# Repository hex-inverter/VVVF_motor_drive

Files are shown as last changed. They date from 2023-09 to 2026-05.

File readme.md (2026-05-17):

# Three-Phase Induction Motor Controller

The inspiration for this project came from a very characteristic sound in Amsterdam metro trams. During acceleration or braking they make a "shifting gears" sound even though the motors are electric (this sound can also be heard in the demonstration video below).
I became interested in what causes this phenomenon and discovered that the sound is related to the switching behavior and frequency management of inverter-driven AC motors. To better understand these systems, I designed and built a complete three-phase induction motor controller and presented a project for seminar class as part of the course at Faculty of Electrical Engineering, University of Ljubljana.

The project focuses on generating variable-frequency three-phase waveforms using SPWM (Sinusoidal Pulse Width Modulation) and DDS (Direct Digital Synthesis) techniques implemented on an STM32 microcontroller. The controller is capable of driving an asynchronous motor directly from rectified mains voltage while allowing the motor speed to be controlled with a potentiometer.

Here you can find a video demonstration of the final product:

<a href="https://youtu.be/MzE1TKPA2_U?si=Al2wI3Vebfvr4Jmp&t=35">
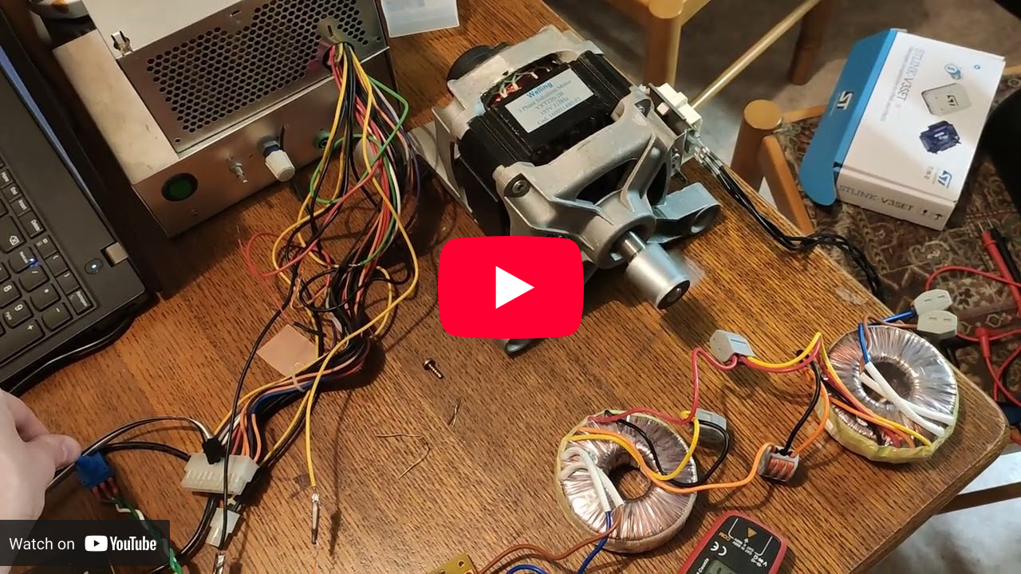
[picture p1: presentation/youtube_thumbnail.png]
    
</a>

## Overview

The controller consists of a mains input stage with EMI filtering, a rectifier that generates a high-voltage DC bus, and a three-phase inverter built using IGBT transistors. The inverter is controlled by an STM32 microcontroller, which generates SPWM drive signals for the motor phases.
Motor speed is adjusted by a potentiometer, while the firmware continuously monitors current and DC bus voltage through ADC measurements. The project also implements different switching strategies to reduce transistor losses at higher output frequencies.

The more in-depth report of the working of the driver can be found in the project report (in Slovenian).

## Hardware

The hardware was designed in KiCad and PCB was etched at home.

<a>
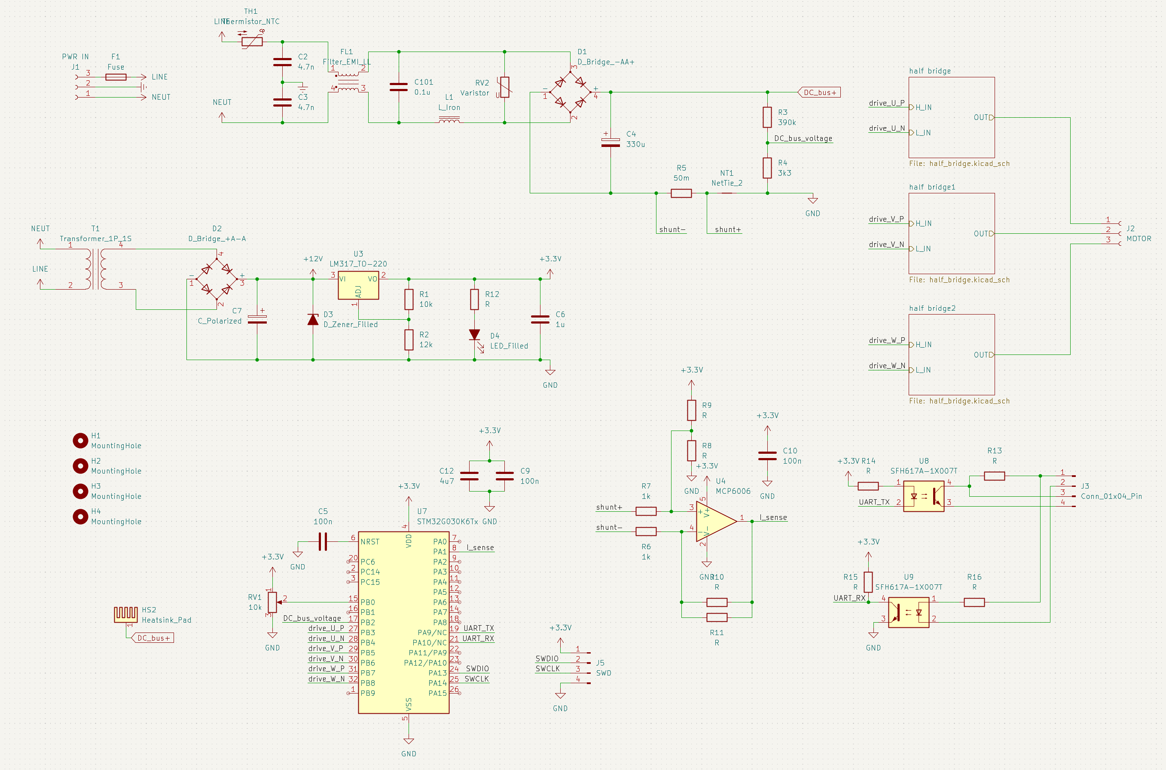
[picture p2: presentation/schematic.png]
    
</a>

Main components:
- EMI filtering
- Mains rectification
- Low-voltage auxiliary power supply
- Three-phase IGBT inverter
- Gate driver circuitry
- Current sensing
- STM32 control circuitry
- Custom PCB

## Firmware

The firmware is written for the STM32G030 microcontroller and generates three-phase SPWM signals for motor control. Frequency generation is implemented using DDS techniques and lookup tables, allowing smooth adjustment of motor speed and phase generation with 120° offsets between phases. The software also handles ADC measurements, frequency management, and inverter switching control.

## Repository Structure

```text
HW/             Hardware design files, schematics, PCB made in KiCad
FW/             STM32 firmware source code
docs/           Documentation and research papers
presentation/   Project report and presentation (sorry, it's in Slovenian)
```

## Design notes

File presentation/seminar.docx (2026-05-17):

Univerza v Ljubljani

Fakulteta za elektrotehniko

Krmilnik trifaznega asinhronskega motorja

Avtor: Boris Trček

Ljubljana, 2023

# 0. Ključne besede

Krmilnik AC motorja, inverter, asinhronski motor, SPWM, DDS

AC motor driver, inverter, asynchronous motor, SPWM, DDS

# 1 Uvod

Nemalokrat sem že opazil, da se nekateri izmenični motorji pri pospeševanju oddajajo nenavaden zvok. Ta namreč med naraščanjem piskanja preskoči na nižjo frekvenco, od koder se ponovno viša. Ponavadi se ta proces tudi večkrat ponovi. Pogosto ga je mogoče slišati pri zaviranju ali pospeševanju tramvajev ali vlakov na podzemnih železnicah. Zanimalo me je zakaj do tega pojava pride, zato sem se odločil da bom za projekt pri predmetu Seminar iz elektronike naredil krmilnik trifaznega motorja.

# 2 Načrtovane specifikacije naprave

Za napravo sem postavil sledeče cilje:

- krmiliti mora trifazni motor s podanimi specifikacijami; nominalna napetost 195V, nominalna frekvenca 310 Hz,
- napajati se mora z omrežno napetostjo 230V 50 Hz,
- delovati mora tako, da se da program enostavno prilagoditi drugemu večfaznemu motorju s spremembo konstant,
- hitrost vrtenja motorja je mogoče krmiliti s potenciometrom.

# 3 Finančni plan

Eden izmed glavnih ciljev projekta je čim cenejša izvedba. Na podlagi tega sem se ubral okolju prijaznejšo rešitev in veliko komponent pridobil z odsluženih vezij starih gospodinjskih aparatov in ostalih naprav.

# 4 Sheme vezja naprave

Spodnji sliki prikazujeta blokovno shemo in shemo krmilnika motorja.

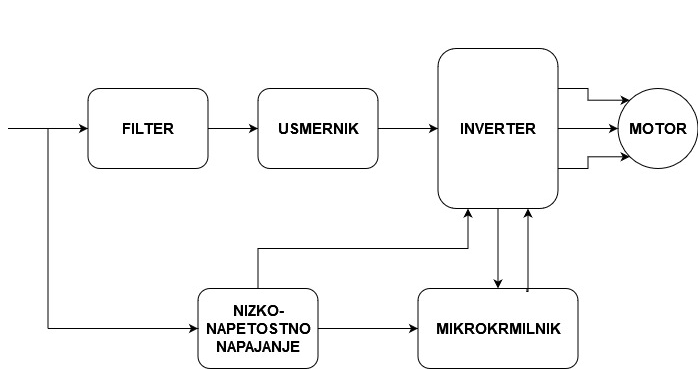
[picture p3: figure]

Slika 1: Blokovna shema


Slika 2: Celotna shema vezja

## 4.1 Filter

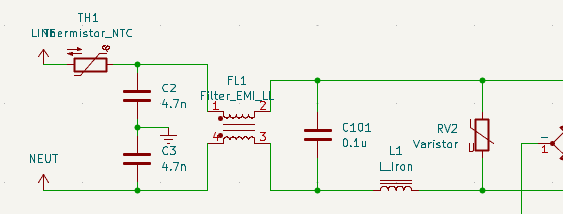
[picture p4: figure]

Slika 3: Filtrirni del vezja

Naprava je napajana z omrežno napetostjo. Takoj pri vhodu se nahajajo filtri, da zmanjša tiste motnje, ki prihajajo v napravo, kot tudi tiste, ki jih naprava generira. NTC termistor z povečano upornostjo preprečuje povečan vhodni tok, ki nastane zaradi polnjenja kondenzatorjev ob zagonu. Za njim dva kondenzatorja tipa Y vrednosti 4,7 nF in dušilka filtrirajo sofazne motnje. Nato kondenzator tipa X velikosti 100 nF zmanjša medfazne motnje. S pomočjo dušilke L1 blažimo tokovne špice, ki nastanejo zaradi polnjenja kondenzatorjev. Z varistorjem RV2 omejimo napetostne sunke.

## 4.2 Usmernik

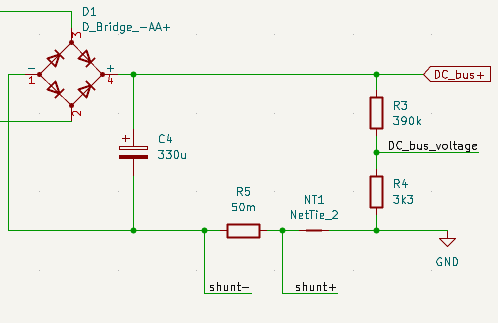
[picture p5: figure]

Slika 4: Usmernik

Usmerniški del vezja sestavljata polnovalni mostiščni usmernik, ki iz sinusnega signala ustvari pozitivno napetost, to pa nato zgladimo z elektrolitskim kondenzatorjem vrednosti 330 µF. Tako pridobimo enosmerno napetostno linijo z amplitudo 325 V, s katero napajamo inverterski del vezja.

## 4.3 Inverter

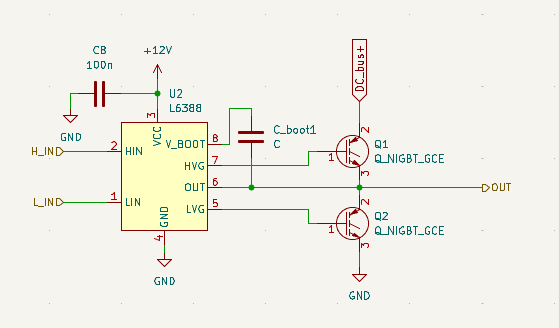
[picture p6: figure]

Slika 5: Inverterski del vezja

Inverter sestavljajo 3 pari IGBT STGP10NC60. Ti tranzistorji imajo v primerjavi z MOSFET nižke izgube in hitrejše preklapljanje. Ker se na njih kljub temu izgublja veliko energije, so skupaj z Grietzovim mostičem usmerniškega dela vezja pritrjeni na hladilna rebra. Tranzistorje krmili mikrokrmilnik preko IGBT krmilnikov. Ta omogoča, da z enim čipom krmilimo vrata obeh tranzistorjev hkrati, kljub temu da lahko napetosti dosežejo tudi do 600V. Omogočajo hitro preklapljanje tranzistorjev, hkrati pa onemogočajo, da bi bila odprta oba tranzistorja hkrati. Takrat bi čez njiju stekel visok tok, zaradi česar bi prišlo do poškodb.

Na srednji odcep vsakega izmed parov tranzistorjev je povezana faza motorja.

## 4.4 Nizkonapetostno napajanje

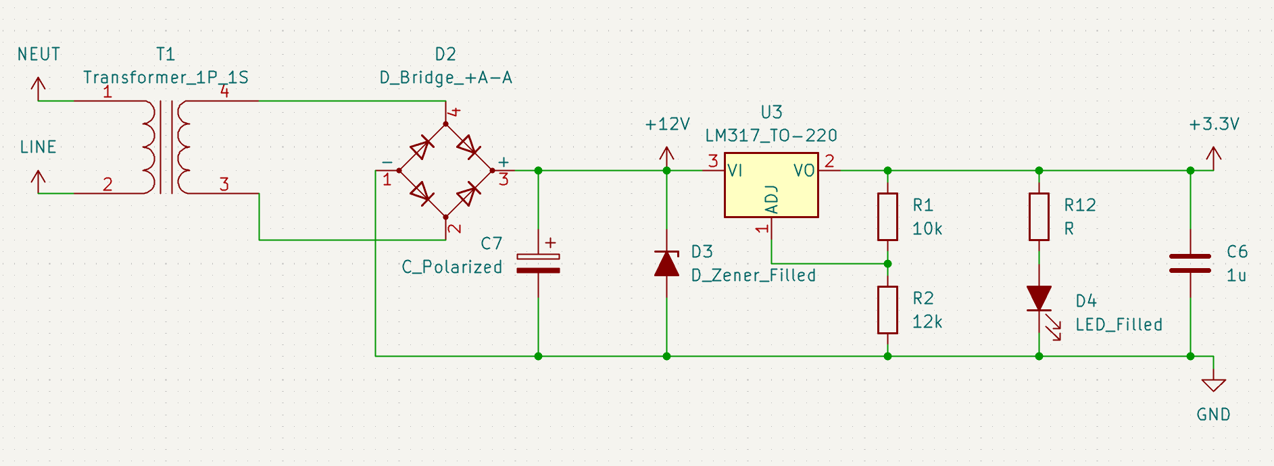
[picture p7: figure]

Slika 6: nizkonapetostno napajanje

S pomočjo transformatorja dobimo iz omrežne napetosti tudi napetost 12V, ki je zglajena in usmerjena s pomočjo polnovalnega mostiščnega usmernika in kondenzatorja. Ker lahko transformator generira tudi višje napetosti, če je premalo obremenjen, sem dodal tudi 15 V zenerjevo diodo. Ta napetost je nato uporabljena za napajanje IGBT krmilnikov in mikrokrmilnika preko linearnega regulatorja, ki zniža napetost na 3.3V.

## 4.5 Mikrokrmilnik

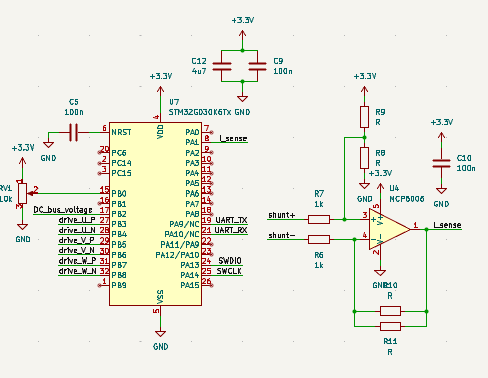
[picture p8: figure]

Slika 7: Mikrokrmilniški del vezja z periferijo

Mikrokrmilnik STM32G030K6T krmili odpiranje in zapiranje tranzistorjev z algoritmom opisanim v naslednjem poglavju glede na željeno frekvenco, ki jo določimo s pozicijo potenciometra. Mikrokrmilnik prav tako upošteva povratno informacijo o toku, ki jo dobi preko tokovnega merilnega upora in operacijskega ojačevalnika, ter napetosti na usmerniku, ki jo izmeri z uporovnega delilnika.

# 5. Tiskano vezje

Spodnje slike prikazujejo zgornjo in spodnjo stran tiskanega vezja, ter končni produkt.

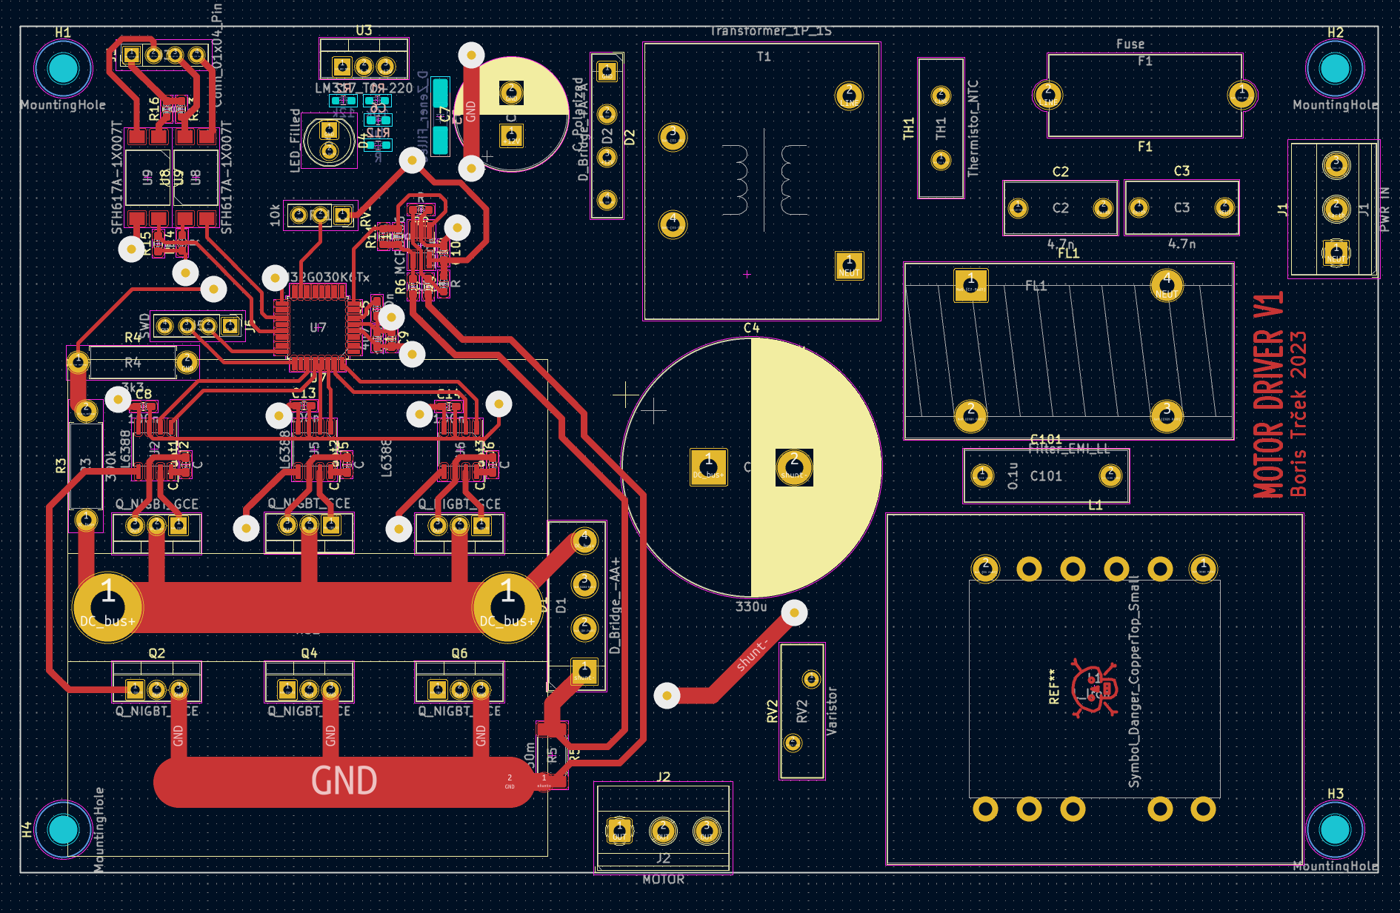
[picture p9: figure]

Slika 8: Zgornja stran tiskanega vezja

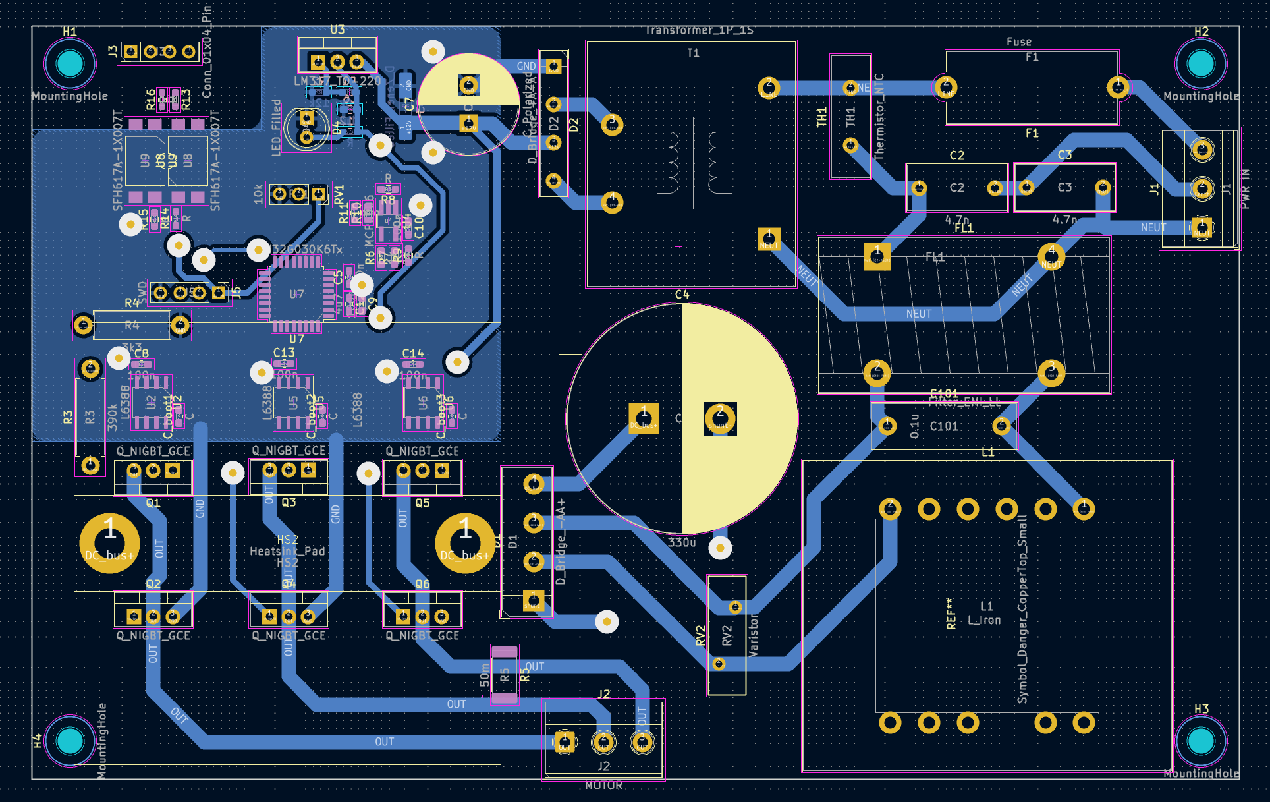
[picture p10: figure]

Slika 9: Spodnja stran tiskanega vezja

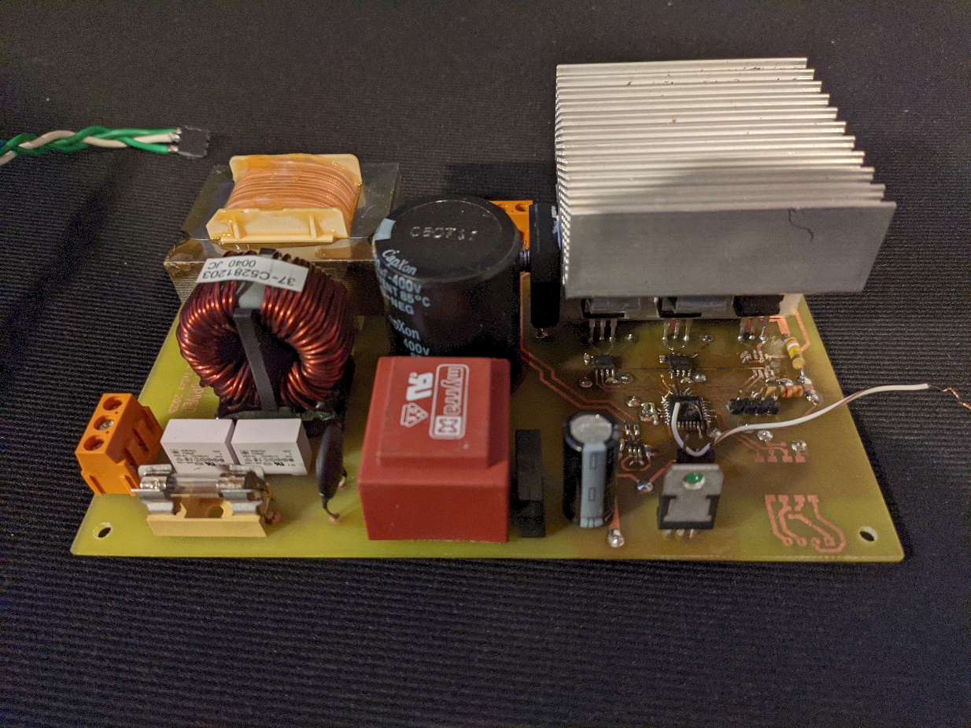
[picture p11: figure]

Slika 10: končni izdelek

# 6. Opis delovanja

Pri krmiljenju motorja z tranzistorji nastane problem, če ga želimo krmiliti z sinusno obliko napetosti. Takrat so namreč tranzistorji delno odprt, motor pa lahko predstavlja visoko breme. Zato se tranzistorji močno segrevajo in lahko tudi pregorijo. Namesto tega se tranzistorje krmili tako, da so ti popolnoma odprti ali zaprti. Da dobimo približek sinusne napetosti pod temi pogoji, moramo uporabiti PWM signal, katerega širina je določena z amplitudo sinusnega signala v določenem časovnem odseku.

## 6.1 SPWM

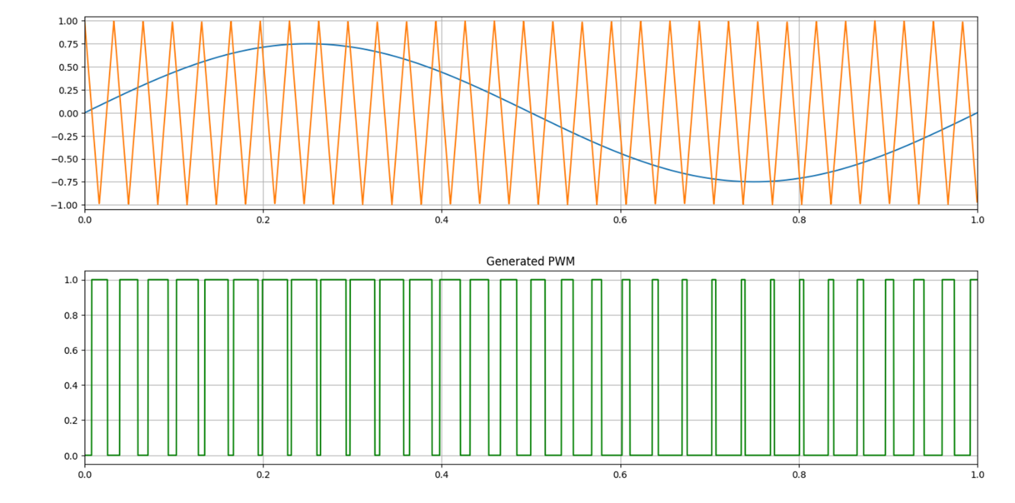
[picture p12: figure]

Slika 11: Generiranje SPWM signala

Postopek za pridobivanje SPWM (Sinusi PWM) signala je razviden iz slike zgornje slike.

Oba tranzistorja se krmili s tem signalom, pri tem pa se signal za krmiljenje spodnjega tranzistorja invertira. Zgornji tranzistor se torej odpre, kadar je sinusni signal večji od vrednosti trikotnega signala, v nasprotnem primeru pa se odpre spodnji tranzistor. Če bi ta signal integrirali po času, bi dobili sinusu podoben signal.

## 6.2 Prestavljanje

Če želimo povečevati hitrost vrtenja motorja, se mora spreminjati frekvenca krmilnega SPWM signala. Tako pridemo do novega problema. Pri višjih frekvencah se na enako gostoto trikotnih signalov znotraj ene periode sinusnega signala tranzistorji pogosteje preklopijo, kar pa poveča tudi izgube na njih, saj so več časa v linearnem področju. Problem je mogoče videti na spodnji sliki.

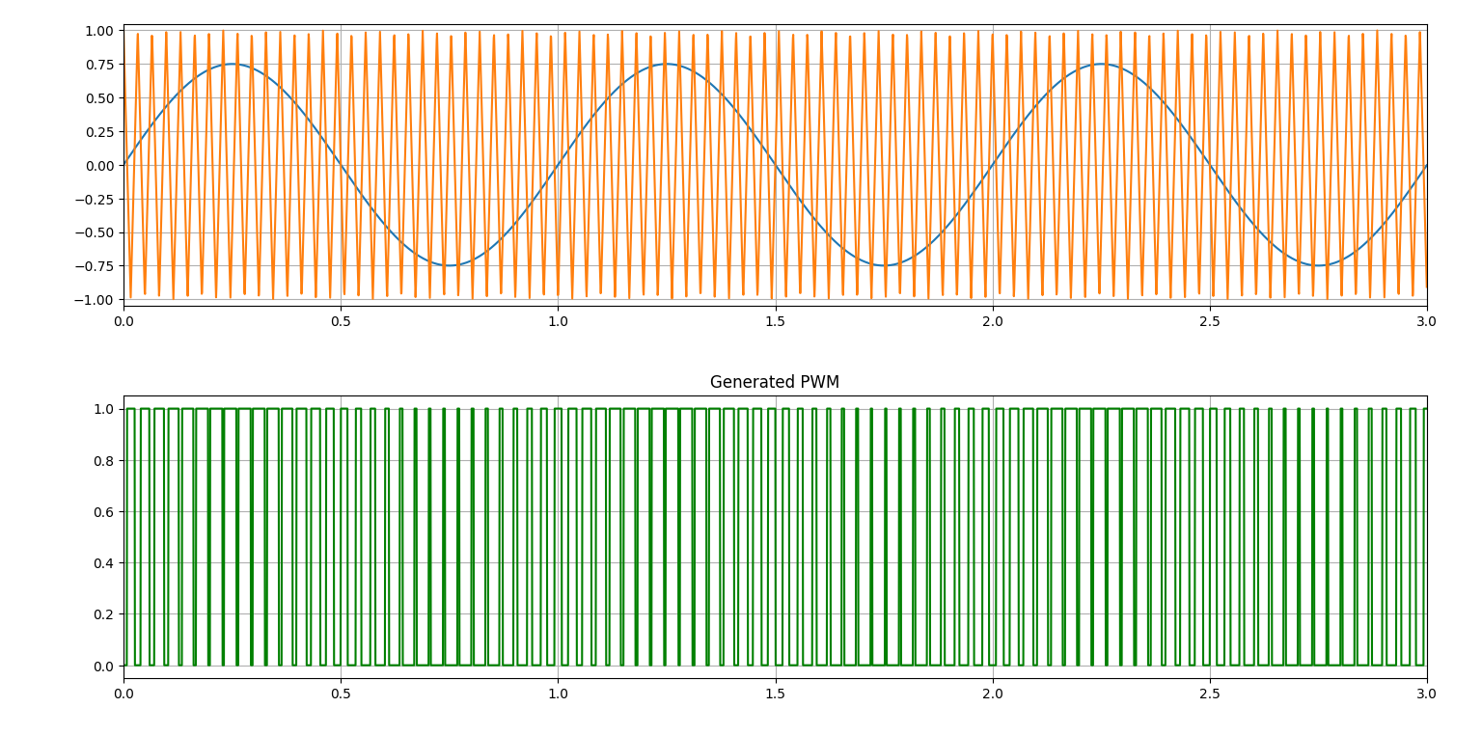
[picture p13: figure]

Slika 12: Primerjava gostote preklopov pri previsokem razmerju period trikotnega in sinusnega signala

Temu se izognemo tako, da zmanjšamo število trikotnikov na periodo sinusnega signala. Temu pojavu se reče "prestavljanje", ki ga je mogoče tudi slišati. Spodnja slika prikazuje kako izgleda izhodni signal pri zmanjšanju razmerja frekvenc signalov.

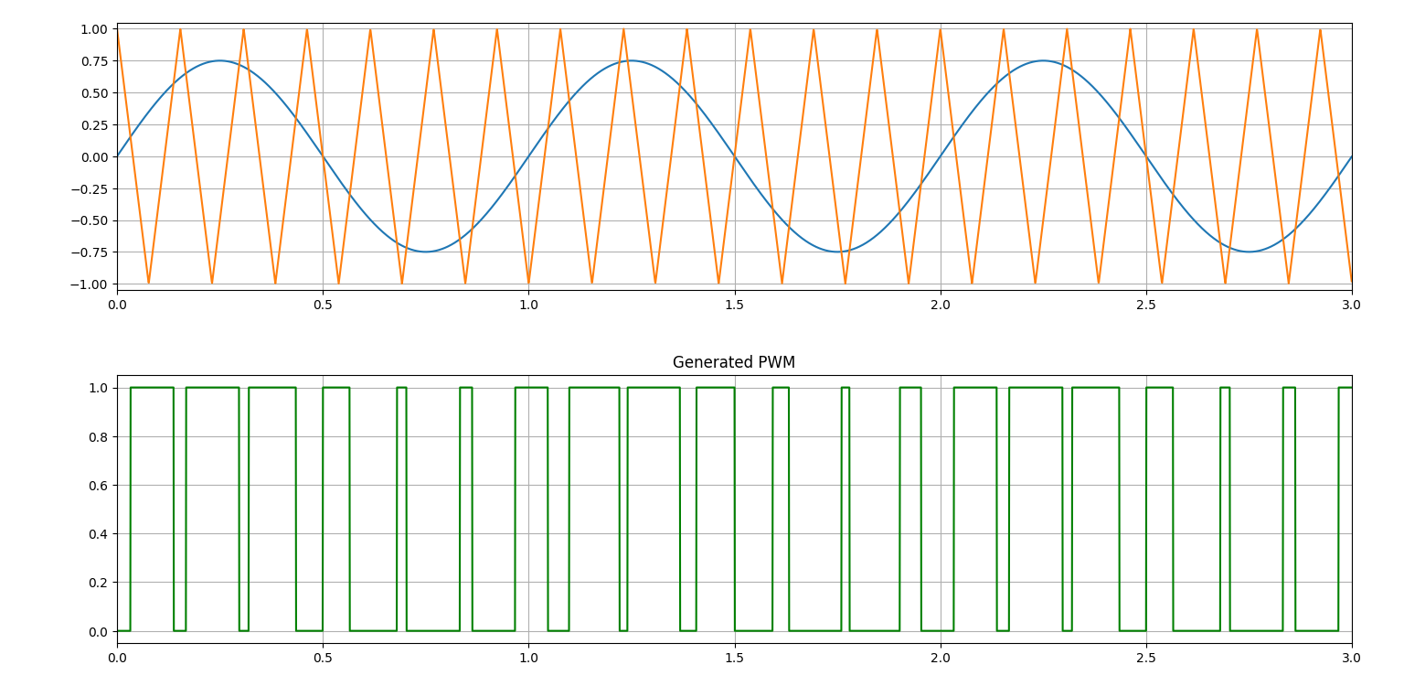
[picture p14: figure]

Slika 13: Primerjava gostote preklopov pri znižanem razmerju period trikotnega in sinusnega signala

## 6.3 Direktna digitalna sinteza (DDS)

DDS (ang. Direct digital synthesis) je metoda za generiranje poljubnega periodičnega signala (pogosto sinusnega) s pomočjo fiksne referenčne frekvence.

Za generiranje SPWM signala sem uporabil 32-bitno število kot fazni akumulator. Potrebna je tudi tabela (ang. array), v kateri imamo shranjen potek signala ene ali polovice periode sinusnega signala. V mojem primeru sem v tabelo dolgo 2¹¹ shranil elemente prve periode SPWM signala.

31 | 30 - 20 | 19 - 0

Tabela 1: Segmentacija 32-bitnega faznega akumulatorja

32-bitni fazni akumulator je razdeljen na 3 segmente. Najpomembnejši bit (ang. MSB) se uporablja kot predznak sinusnega vala v tem trenutku. Na podlagi tega bomo invertirali vhodni signal tranzistorjev pri negativnem valu sinusnega signala. Naslednjih 11 bitov predstavlja kazalec (ang. pointer) na določen element v preje omenjeni tabeli. Ostalih 20 bitov je ostanek.

Ob vsakem pulzu sinusnega signala sem prištel faznemu akumulatorju neko vrednost, ki je odvisna od trenutne frekvence. Višja kot je trenutna frekvenca, večje število prištevamo akumulatorju. Tako se odvisno od trenutne frekvence spreminja hitrost premikanja po tabeli. Ostanek 20 bitov nam omogoča, da se po tabeli premikamo počasneje od enega koraka na referenčni pulz, saj se manjše vrednosti akumulirajo in lahko do skoka na naslednji korak v tabeli pride šele po več pulzih. Ostanek nam torej poveča resolucijo frekvence.

Zaradi manjšanja števila trikotnikov pri višjih frekvencah, kot je bilo opisano v podpoglavju 6.2 Prestavljanje, je shranjenih več tabel. Glede na trenutno frekvenco se lahko spremeni osnovni kazalec na tabelo, temu pa se prišteva odmik kazalca na element v tabeli.

# 7. Potek programa

Spodnja slika prikazuje diagram poteka programa.

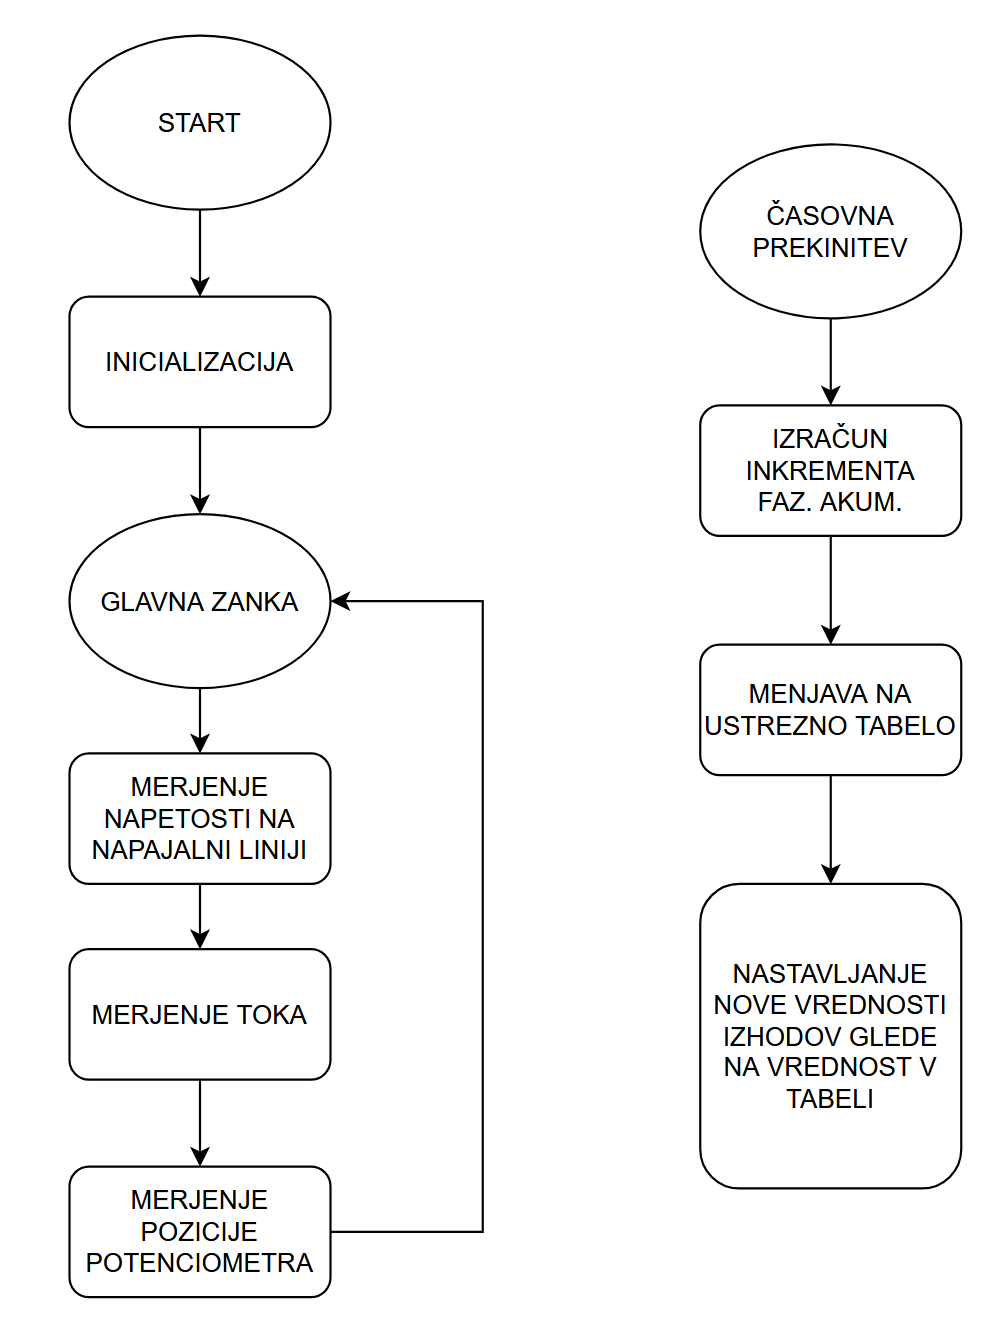
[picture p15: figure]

Slika 14: diagram poteka programa

Ko se mikrokrmilnik zažene, se najprej inicializirajo sistemska ura, časnovnik, GPIO in ADC. Nato v glavni zanki beremo vrednost ADC, preračunamo in shranimo vrednosti za napajalno napetost inverterja, tok in pozicijo potenciometra. S tem se izognemo branju ADC v časovni prekinitvi, saj ti trajajo precej dolgo.

Časovnik proži prekinitev z referenčno frekvenco. Ob vsaki prekinitvi izračunamo za koliko se mora povečati akumulator faze glede na trenutno izbrano frekvenco potenciometra. Če je trenutna frekvenca previsoka, zamenjamo na katero tabelo kaže kazalec.

Iz akumulatorja frekvence izluščimo zamik kazalca na tabelo. Vsota kazalca na tabelo in zamika nam pove v kateri poziciji mora bit transistor. Postopek ponovimo še za ostala para tranzistorjev tako, da trenutni vsoti kazalca prištejemo še 1/3 in 2/3 dolžine tabele, saj se faze med seboj razlikujejo za 120°. Glede na razbrane vrednosti postavimo ustrezne GPIO izhode.

# 8. Navodila za uporabo

Napravo priključimo na omrežno napetost. S spremembo pozicije osi potenciometra nastavimo željeno hitrost vrtenja motorja.

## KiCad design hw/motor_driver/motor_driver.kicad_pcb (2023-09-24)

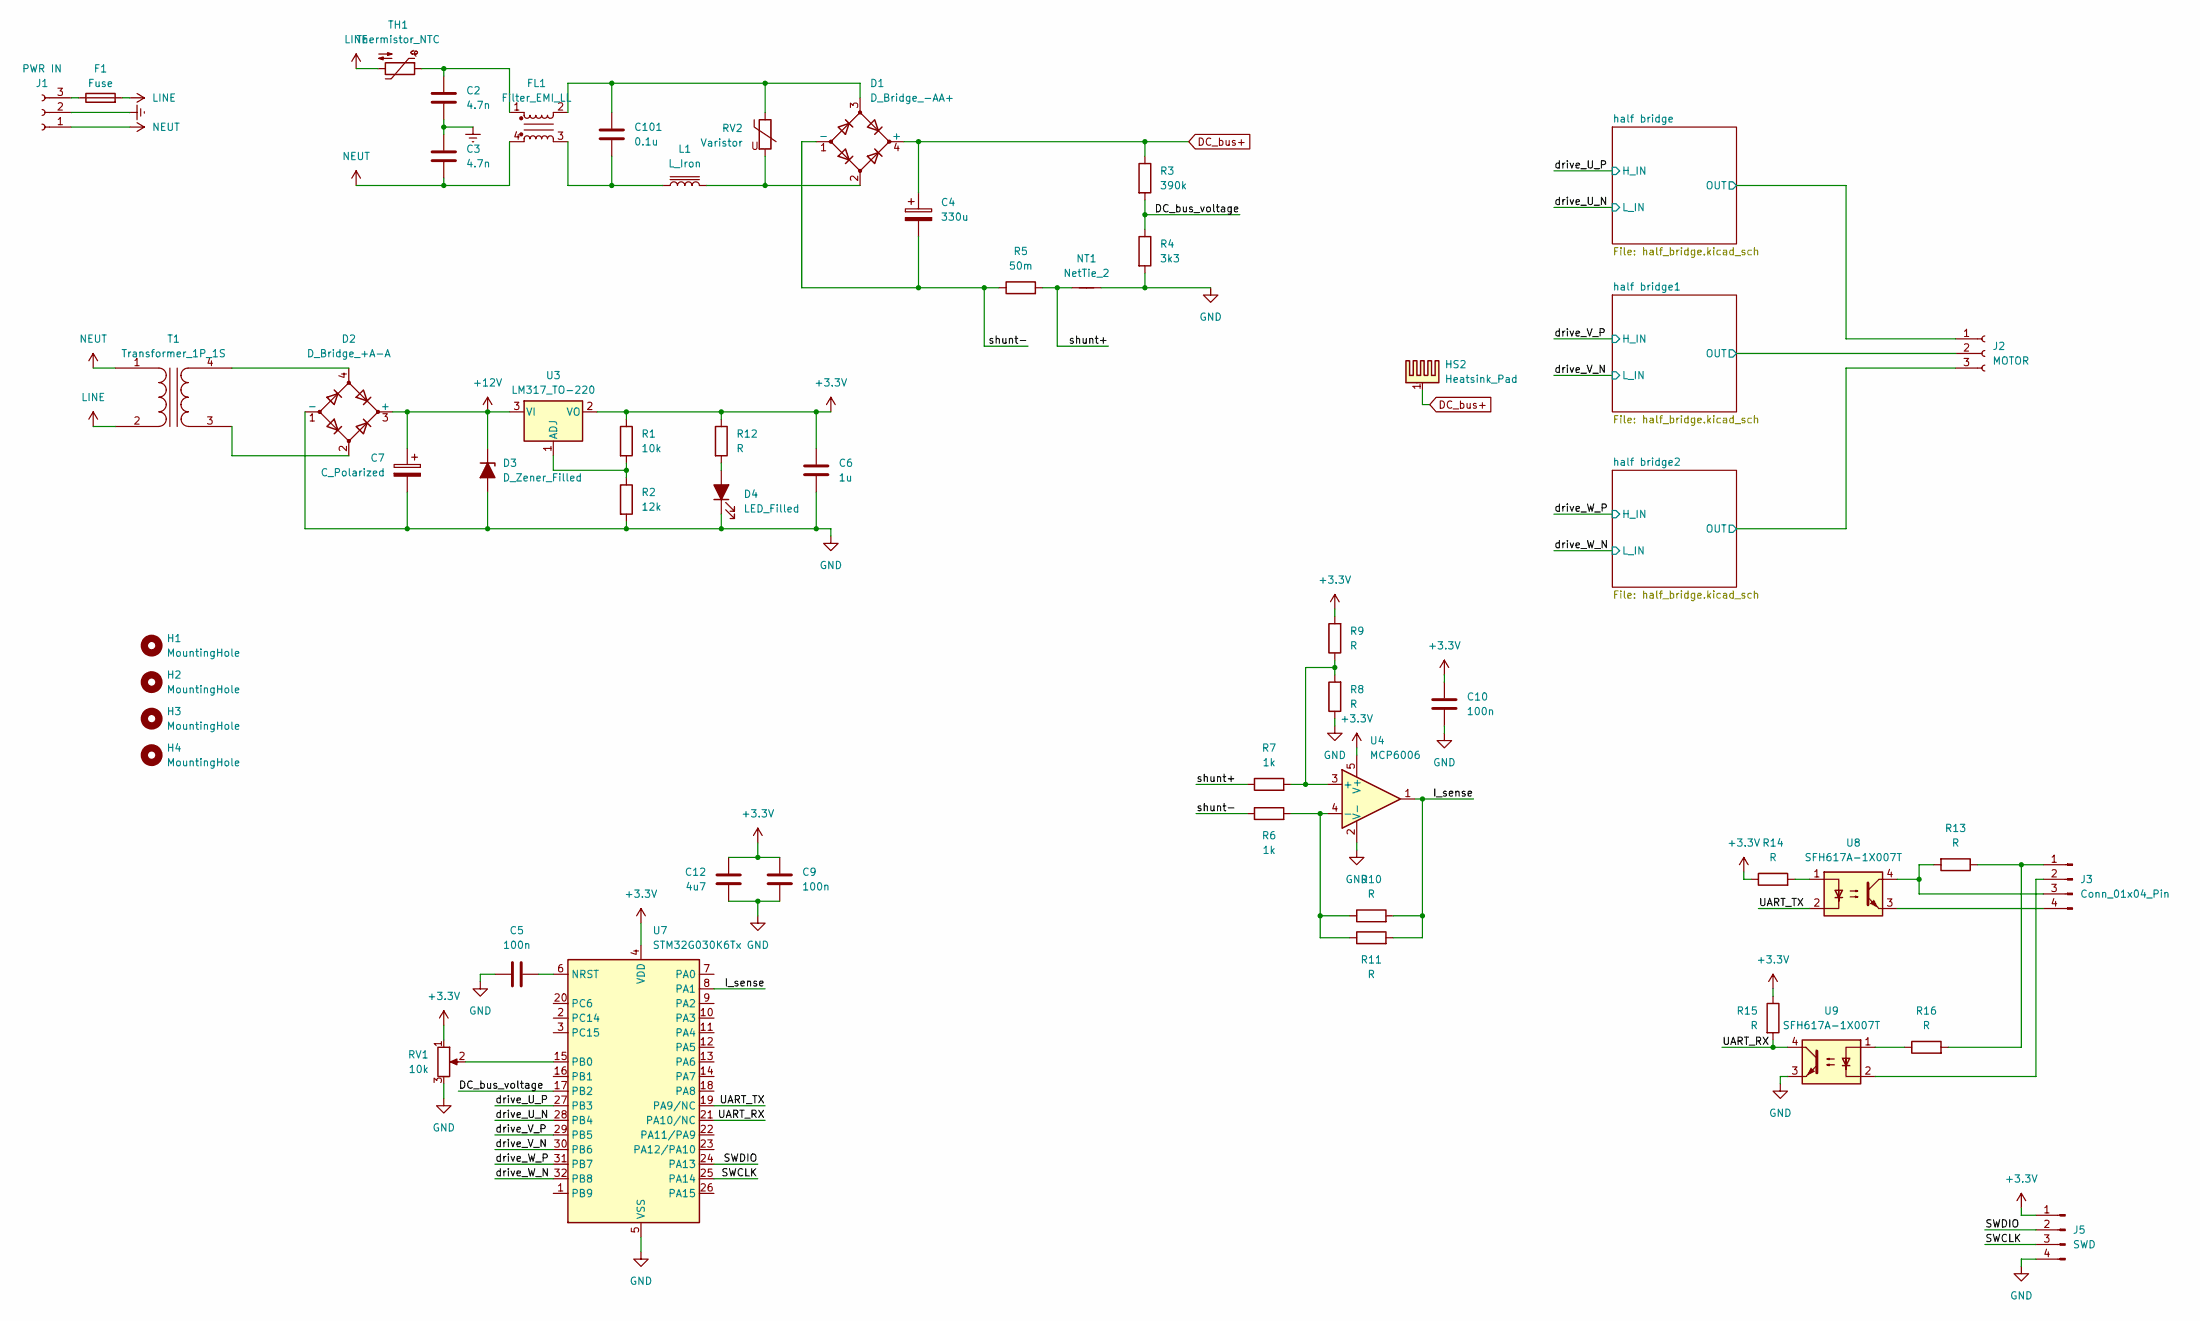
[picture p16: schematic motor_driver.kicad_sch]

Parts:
C2, C3: 4.7n; C_Rect_L13.0mm_W6.0mm_P10.00mm_FKS3_FKP3_MKS4
C4: 330u; CP_Radial_D30.0mm_P10.00mm_SnapIn
C5, C9, C10: 100n; C_0603_1608Metric_Pad1.08x0.95mm_HandSolder
C6: 1u; C_0603_1608Metric_Pad1.08x0.95mm_HandSolder
C7: C_Polarized; CP_Radial_D13.0mm_P5.00mm
C12: 4u7; C_0603_1608Metric_Pad1.08x0.95mm_HandSolder
C101: 0.1u; C_Rect_L19.0mm_W6.0mm_P15.00mm_MKS4
D1: D_Bridge_-AA+; Diode_Bridge_Vishay_KBL
D2: D_Bridge_+A-A; Diode_Bridge_19.0x3.5x10.0mm_P5.0mm
D3: D_Zener_Filled; D_MiniMELF_Handsoldering
D4: LED_Filled; LED_D5.0mm
F1: Fuse; Fuseholder_Cylinder-5x20mm_Stelvio-Kontek_PTF78_Horizontal_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
FL1: Filter_EMI_LL; L_CommonMode_Toroid_Vertical_L38.1mm_W20.3mm_Px15.24mm_Py22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
H1, H2, H3, H4: MountingHole; MountingHole_3.2mm_M3
HS2: Heatsink_Pad; heatsink_56x58
J1: PWR IN; TerminalBlock_Phoenix_MKDS-1,5-3-5.08_1x03_P5.08mm_Horizont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
J2: MOTOR; TerminalBlock_Phoenix_MKDS-1,5-3-5.08_1x03_P5.08mm_Horizont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
J3: Conn_01x04_Pin; PinHeader_1x04_P2.54mm_Vertical
J5: SWD; PinHeader_1x04_P2.54mm_Vertical
L1: L_Iron; Coil_40x48
NT1: NetTie_2; NetTie-2_SMD_Pad2.0mm
R1: 10k; R_0603_1608Metric_Pad0.98x0.95mm_HandSolder
R2: 12k; R_0603_1608Metric_Pad0.98x0.95mm_HandSolder
R3: 390k; R_Axial_DIN0411_L9.9mm_D3.6mm_P12.70mm_Horizontal
R4: 3k3; R_Axial_DIN0411_L9.9mm_D3.6mm_P12.70mm_Horizontal
R5: 50m; R_2512_6332Metric_Pad1.40x3.35mm_HandSolder
R6, R7: 1k; R_0603_1608Metric_Pad0.98x0.95mm_HandSolder
R8, R9, R10, R11, R12, R13, R14, R15, R16: R; R_0603_1608Metric_Pad0.98x0.95mm_HandSolder
RV1: 10k; PinSocket_1x03_P2.54mm_Vertical
RV2: Varistor; RV_Disc_D15.5mm_W4.9mm_P7.5mm
T1: Transformer_1P_1S; transformer_12V
TH1: Thermistor_NTC; C_Disc_D16.0mm_W5.0mm_P7.50mm
U3: LM317_TO-220; TO-220-3_Vertical
U4: MCP6006; TSOT-23-5_HandSoldering
U7: STM32G030K6Tx; LQFP-32_7x7mm_P0.8mm
U8, U9: SFH617A-1X007T; SMDIP-4_W9.53mm_Clearance8mm

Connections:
+3.3V: C6.1, C9.2, C10.2, C12.2, J5.1, R1.1, R9.2, R12.1, R14.1, R15.1, RV1.1, U3.2 (VO), U4.5 (V+), U7.4 (VDD)
+12V: C7.1, D2.3 (+), D3.1 (K), U3.3 (VI); also elsewhere on the board
/DC_bus_voltage: R3.2, R4.1, U7.17 (PB2)
/I_sense: R10.2, R11.2, U4.1, U7.8 (PA1)
/SWCLK: J5.3, U7.25 (PA14)
/SWDIO: J5.2, U7.24 (PA13)
/UART_RX: R15.2, U7.21 (PA10/NC), U9.4
/UART_TX: U7.19 (PA9/NC), U8.2
/drive_U_N: U7.28 (PB4); also elsewhere on the board
/drive_U_P: U7.27 (PB3); also elsewhere on the board
/drive_V_N: U7.30 (PB6); also elsewhere on the board
/drive_V_P: U7.29 (PB5); also elsewhere on the board
/drive_W_N: U7.32 (PB8); also elsewhere on the board
/drive_W_P: U7.31 (PB7); also elsewhere on the board
/half bridge1/OUT: J2.2; also elsewhere on the board
/half bridge2/OUT: J2.3; also elsewhere on the board
/half bridge/OUT: J2.1; also elsewhere on the board
/shunt+: NT1.1, R5.2, R7.1
/shunt-: C4.2, D1.1 (-), R5.1, R6.1
DC_bus+: C4.1, D1.4 (+), HS2.1, R3.1; also elsewhere on the board
Earth: C2.2, C3.1, J1.2
GND: C5.1, C6.2, C7.2, C9.1, C10.1, C12.1, D2.1 (-), D3.2 (A), D4.1 (K), J5.4, NT1.2, R2.2, R4.2, R8.1, RV1.3, U4.2 (V-), U7.5 (VSS), U9.3; also elsewhere on the board
LINE: F1.2, T1.2 (AB), TH1.2
NEUT: C3.2, FL1.4, J1.1, T1.1 (AA)
unnamed: C2.1, FL1.1, TH1.1
unnamed: C101.1, D1.3, FL1.2, RV2.1
unnamed: C101.2, FL1.3, L1.1
unnamed: D1.2, L1.2, RV2.2
unnamed: D4.2 (A), R12.2
unnamed: F1.1, J1.3
unnamed: J3.1, R13.1, R16.2
unnamed: J3.2, U9.2
unnamed: J3.3, R13.2, U8.4
unnamed: J3.4, U8.3
unnamed: R14.2, U8.1
unnamed: R16.1, U9.1
unnamed: D2.2, T1.3 (SA)
unnamed: D2.4, T1.4 (SB)
unnamed: R1.2, R2.1, U3.1 (ADJ)
unnamed: R7.2, R8.2, R9.1, U4.3 (+)
unnamed: R6.2, R10.1, R11.1, U4.4 (-)
unnamed: C5.2, U7.6 (NRST)
unnamed: RV1.2, U7.15 (PB0)

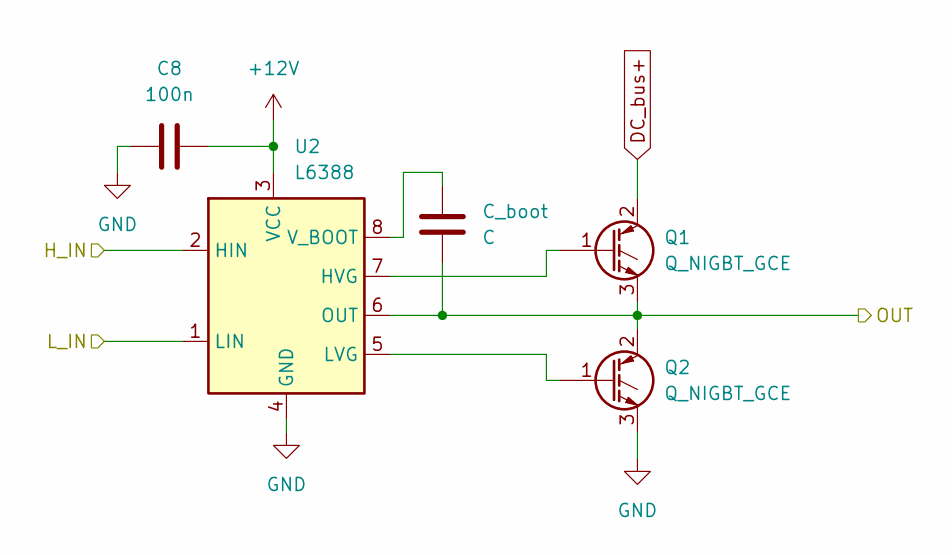
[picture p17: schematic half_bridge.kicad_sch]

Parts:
C8: 100n; C_0603_1608Metric_Pad1.08x0.95mm_HandSolder
C_boot: C; C_0603_1608Metric_Pad1.08x0.95mm_HandSolder
Q1, Q2: Q_NIGBT_GCE; TO-220-3_Vertical
U2: L6388; SO-8_3.9x4.9mm_P1.27mm

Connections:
+12V: C8.2, U2.3 (VCC); also elsewhere on the board
/drive_U_N: U2.1 (LIN); also elsewhere on the board
/drive_U_P: U2.2 (HIN); also elsewhere on the board
/half bridge/OUT: Q1.3 (E), Q2.2 (C), U2.6 (OUT); also elsewhere on the board
DC_bus+: Q1.2 (C); also elsewhere on the board
GND: C8.1, Q2.3 (E), U2.4 (GND); also elsewhere on the board
unnamed: Q1.1 (G), U2.7 (HVG)
unnamed: Q2.1 (G), U2.5 (LVG)
unnamed 44: U2.8 (V_BOOT); also elsewhere on the board

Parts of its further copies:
C13, C14: 100n; C_0603_1608Metric_Pad1.08x0.95mm_HandSolder
C_boot1, C_boot2, C_boot3: C; C_0603_1608Metric_Pad1.08x0.95mm_HandSolder
Q3, Q4, Q5, Q6: Q_NIGBT_GCE; TO-220-3_Vertical
U5, U6: L6388; SO-8_3.9x4.9mm_P1.27mm

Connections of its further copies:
+12V: C13.2, C14.2, U5.3 (VCC), U6.3 (VCC); also elsewhere on the board
/drive_V_N: U5.1 (LIN); also elsewhere on the board
/drive_V_P: U5.2 (HIN); also elsewhere on the board
/drive_W_N: U6.1 (LIN); also elsewhere on the board
/drive_W_P: U6.2 (HIN); also elsewhere on the board
/half bridge1/OUT: C_boot2.2, Q3.3 (E), Q4.2 (C), U5.6 (OUT); also elsewhere on the board
/half bridge2/OUT: C_boot3.2, Q5.3 (E), Q6.2 (C), U6.6 (OUT); also elsewhere on the board
/half bridge/OUT: C_boot1.2; also elsewhere on the board
DC_bus+: Q3.2 (C), Q5.2 (C); also elsewhere on the board
GND: C13.1, C14.1, Q4.3 (E), Q6.3 (E), U5.4 (GND), U6.4 (GND); also elsewhere on the board
unnamed: Q3.1 (G), U5.7 (HVG)
unnamed: Q4.1 (G), U5.5 (LVG)
unnamed: Q5.1 (G), U6.7 (HVG)
unnamed: Q6.1 (G), U6.5 (LVG)
unnamed 44: C_boot1.1; also elsewhere on the board
unnamed: C_boot2.1, U5.8 (V_BOOT)
unnamed: C_boot3.1, U6.8 (V_BOOT)

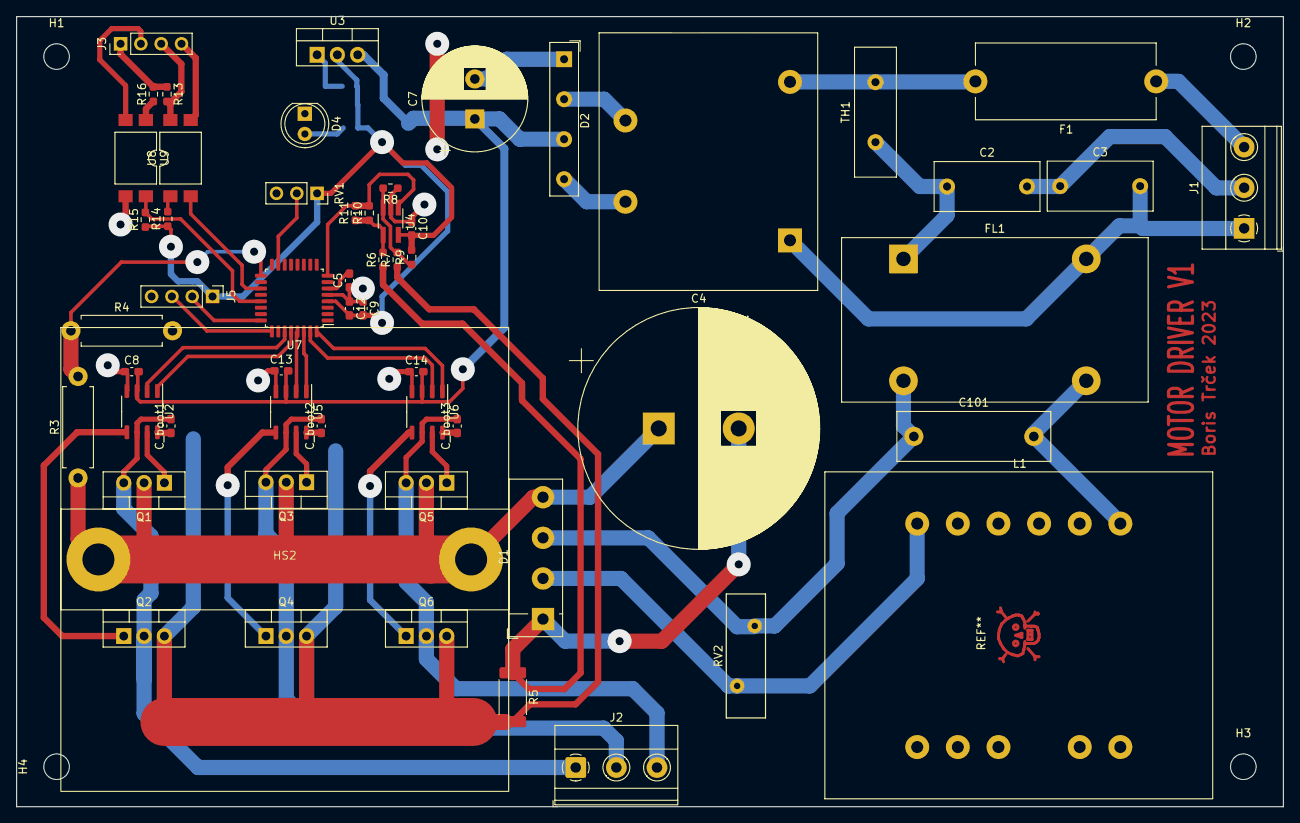
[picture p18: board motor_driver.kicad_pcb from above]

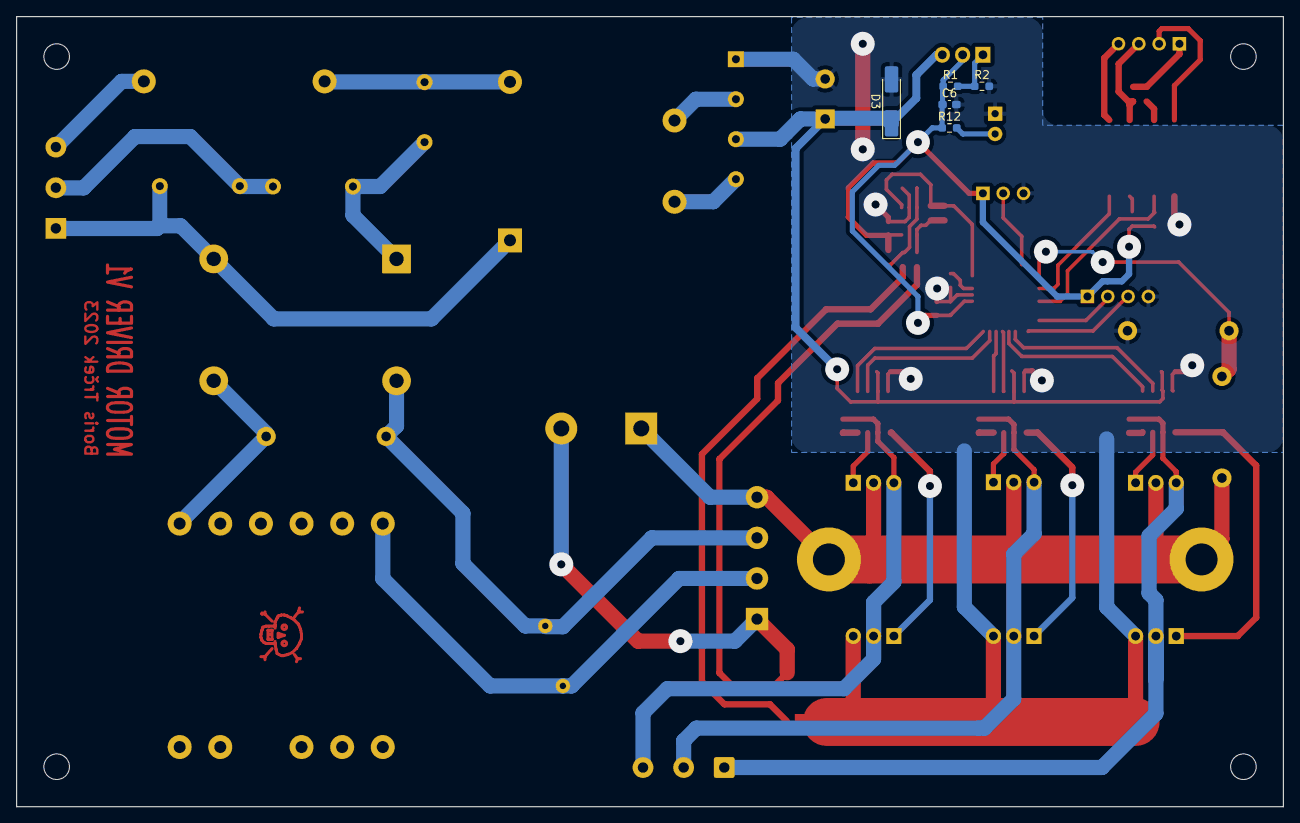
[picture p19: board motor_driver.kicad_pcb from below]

Board: 2 copper layers, 158.4 x 98.8 mm, 67 parts (5 on the bottom side), 52 nets.

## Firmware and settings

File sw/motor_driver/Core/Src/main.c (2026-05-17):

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
/* Includes ------------------------------------------------------------------*/
#include "main.h"

/* USER CODE BEGIN Includes */
#include "pwm_tables.h"
/* USER CODE END Includes */

/* USER CODE BEGIN PTD */

typedef struct ADC_meas_s{
	uint32_t current;
	uint32_t pot;
	uint32_t voltage;
} ADC_meas_t;

/* USER CODE END PTD */

/* USER CODE BEGIN PD */

//volatile uint8_t LED_STATE = 0;

const uint32_t CLK_FREQ = 64000000;
//const uint32_t MAX_I_SHTDWN = 1500; /* in mA */
const uint32_t MAX_I_SHTDWN = 3500; /* in mA */
const uint32_t F_MAX = 200; /* in Hz */
const uint32_t F_MIN = 2;
const int32_t DELTA_F_UP = 5; // units of 2^16/65507 (almost 1) Hz/s
const int32_t DELTA_F_DN = -10;
const uint32_t PERIOD_FULL = UINT32_MAX;
const uint32_t PERIOD_ONE_THIRD = PERIOD_FULL / 3;
const uint32_t PERIOD_TWO_THIRD = PERIOD_FULL / 3 * 2;

#define TIM_DIV 977
const uint32_t TIM_TRIG_FREQ = CLK_FREQ / TIM_DIV; // approx 65507 Hz, input 2^16 step for 1 Hz

const uint32_t U_NOM = 195; // HACK
const uint32_t F_NOM = 310;

// 191156419 = sqrt(2) (peak) * 4096 (ADC) * 3300 (R2) * 10 (VDD=34/10)
const uint32_t VF_MAGIC_NUMBER = 589303; //191156419 << 16 * U_NOM / (F_NOM * 34 * 393300);

/* USER CODE END PD */


/* USER CODE BEGIN PV */

ADC_meas_t adc_meas;


/* this is a NCO
 * word structure:
 * [31][30 - 20][19 - 0]
 *  │      │        └ remainder
 *  │      └ pointer to the element in LUT
 *  └ Sign determines if wave is currently in positive or negative half
 */
uint32_t phase_accumulator;

volatile uint32_t f_target; // in (2^-16) Hz
volatile uint32_t vf_coef;

uint8_t *p_current_table;
uint16_t current_gear;

uint32_t i_offset = 0;

uint32_t i_meas;



/* USER CODE END PV */

void SystemClock_Config(void);
static void MX_GPIO_Init(void);
static void MX_TIM1_Init(void);
static void MX_ADC1_Init(void);
/* USER CODE BEGIN PFP */

void switch_table(int8_t change);
void increment_accumulator(void);
void motor_disconnect(void);
uint32_t min(uint32_t x, uint32_t y);

/* USER CODE END PFP */

/**
  * @brief  The application entry point.
  * @retval int
  */
int main(void)
{
  /* MCU Configuration--------------------------------------------------------*/

  /* Reset of all peripherals, Initializes the Flash interface and the Systick. */
  LL_APB2_GRP1_EnableClock(LL_APB2_GRP1_PERIPH_SYSCFG);
  LL_APB1_GRP1_EnableClock(LL_APB1_GRP1_PERIPH_PWR);

  /* SysTick_IRQn interrupt configuration */
  NVIC_SetPriority(SysTick_IRQn, 3);

  /* Configure the system clock */
  SystemClock_Config();

  /* Initialize all configured peripherals */
  MX_GPIO_Init();
  MX_TIM1_Init();
  MX_ADC1_Init();
  /* USER CODE BEGIN 2 */

  LL_GPIO_WriteOutputPort(GPIOB, (1 << 8) | (1 << 6) | (1 << 4) );


  volatile uint32_t count = CLK_FREQ / 5;
  while(count--)
  {
	  __NOP();
  }

  /*read current*/
  LL_ADC_ClearFlag_CCRDY(ADC1);
  LL_ADC_ClearFlag_EOC(ADC1);
  ADC1->CHSELR = (1 << 1);
  while(LL_ADC_IsActiveFlag_CCRDY(ADC1) == 0);
  LL_ADC_ClearFlag_CCRDY(ADC1);
  LL_ADC_Enable(ADC1);
  while(LL_ADC_IsActiveFlag_ADRDY(ADC1) == 0);
  LL_ADC_ClearFlag_ADRDY(ADC1);
  LL_ADC_REG_StartConversion(ADC1);
  while(LL_ADC_IsActiveFlag_EOC(ADC1) == 0);
  LL_ADC_ClearFlag_EOC(ADC1);
  LL_ADC_Disable(ADC1);
  adc_meas.current = LL_ADC_REG_ReadConversionData12(ADC1);

  /*read voltage*/
  ADC1->CHSELR = (1 << 10);
  while(LL_ADC_IsActiveFlag_CCRDY(ADC1) == 0);
  LL_ADC_ClearFlag_CCRDY(ADC1);
  LL_ADC_Enable(ADC1);
  while(LL_ADC_IsActiveFlag_ADRDY(ADC1) == 0);
  LL_ADC_ClearFlag_ADRDY(ADC1);
  LL_ADC_REG_StartConversion(ADC1);
  while(LL_ADC_IsActiveFlag_EOC(ADC1) == 0);
  LL_ADC_ClearFlag_EOC(ADC1);
  LL_ADC_Disable(ADC1);
  adc_meas.voltage = LL_ADC_REG_ReadConversionData12(ADC1);



  LL_TIM_EnableIT_UPDATE(TIM1);
  LL_TIM_EnableCounter(TIM1);


  /* USER CODE END 2 */

  /* Infinite loop */
  /* USER CODE BEGIN WHILE */
  while (1)
  {
		/* convert ADC values
		 *
		 * V_meas = ( Vref * ADC_data / ADC_resolution) * ( (R2 + R1) / R2 )
		 * I_meas = Uref * ADC_data / ( ADC_resolution * R_shunt * A_opamp)
		 */

		/*read current*/
		ADC1->CHSELR = (1 << 1);
		while(LL_ADC_IsActiveFlag_CCRDY(ADC1) == 0);
		LL_ADC_ClearFlag_CCRDY(ADC1);
		LL_ADC_Enable(ADC1);
		while(LL_ADC_IsActiveFlag_ADRDY(ADC1) == 0);
		LL_ADC_ClearFlag_ADRDY(ADC1);
		LL_ADC_REG_StartConversion(ADC1);
		while(LL_ADC_IsActiveFlag_EOC(ADC1) == 0);
		LL_ADC_ClearFlag_EOC(ADC1);
		LL_ADC_Disable(ADC1);
		adc_meas.current = LL_ADC_REG_ReadConversionData12(ADC1);


		i_meas = ((3300 / 22 * 20) * adc_meas.current) / (1<<12); /* in mA */
		/*check if current is too high */
		if(i_meas > MAX_I_SHTDWN)
		{
			Error_Handler();
		}


		/*read pot*/
		ADC1->CHSELR = (1 << 8);
		while(LL_ADC_IsActiveFlag_CCRDY(ADC1) == 0);
		LL_ADC_ClearFlag_CCRDY(ADC1);
		LL_ADC_Enable(ADC1);
		while(LL_ADC_IsActiveFlag_ADRDY(ADC1) == 0);
		LL_ADC_ClearFlag_ADRDY(ADC1);
		LL_ADC_REG_StartConversion(ADC1);
		while(LL_ADC_IsActiveFlag_EOC(ADC1) == 0);
		LL_ADC_ClearFlag_EOC(ADC1);
		LL_ADC_Disable(ADC1);
		adc_meas.pot = LL_ADC_REG_ReadConversionData12(ADC1);

		/* calculate target frequency */
		f_target = adc_meas.pot * F_MAX * (1 << 4); // adc goes to 12 bits, 1 Hz is 16 bits
		if(f_target < (F_MIN * (1 << 16))) {
			f_target = F_MIN * (1 << 16);
		}

		/*read voltage*/
		ADC1->CHSELR = (1 << 10);
		while(LL_ADC_IsActiveFlag_CCRDY(ADC1) == 0);
		LL_ADC_ClearFlag_CCRDY(ADC1);
		LL_ADC_Enable(ADC1);
		while(LL_ADC_IsActiveFlag_ADRDY(ADC1) == 0);
		LL_ADC_ClearFlag_ADRDY(ADC1);
		LL_ADC_REG_StartConversion(ADC1);
		while(LL_ADC_IsActiveFlag_EOC(ADC1) == 0);
		LL_ADC_ClearFlag_EOC(ADC1);
		LL_ADC_Disable(ADC1);
		adc_meas.voltage = LL_ADC_REG_ReadConversionData12(ADC1);


		// calculate the V/f coefficient so the ISR can determine the voltage
//		vf_coef = VF_MAGIC_NUMBER / adc_meas.voltage; // TODO
//		vf_coef = 179; // multiplied by 256
		vf_coef = 728; // for 30 V DC bus


//		v_meas = 3300 * adc_meas.voltage * (39120 + 336) / 336 / (1<<12); /* in mV */
		/* USER CODE END WHILE */

		/* USER CODE BEGIN 3 */
  }
  /* USER CODE END 3 */
}

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
/* USER CODE BEGIN 4 */

void switch_table(int8_t change)
{
	/* check for border cases outside this function */
	current_gear += change;
	p_current_table = pwm_table_ptrs[current_gear];
}

void increment_accumulator(void)
{
	static uint32_t f_current;
//	LL_GPIO_SetOutputPin(GPIOB, (1<<1));

	/* calculate new frequency */
	/* is frequency increasing or decreasing? */
	const int32_t f_diff = f_target - f_current;

	if(f_diff > DELTA_F_UP)
	{
		f_current += DELTA_F_UP;
	}
	else if (f_diff < DELTA_F_DN)
	{
		f_current += DELTA_F_DN;
	}
	else
	{
		f_current += f_diff;
	}


	/* check if gear switch is needed */
	if( (current_gear != (NUM_OF_TABLES-1)) && (f_current > pwm_max_freq[current_gear]) )
	{
		switch_table(1);
	}
	else if( (current_gear != 0) && (f_current < pwm_max_freq[current_gear-1]) )
	{
		switch_table(-1);
	}


	/* increment phase accumulator */
	phase_accumulator += f_current;


	// determine modulation index
//	uint32_t threshold = (vf_coef * f_current) >> 24; // 16b from freq, 8b from vf_coef
//	if (threshold < 2) {
//		// TODO: base boost?
//		threshold = 2; // TODO: calculate this?, change for full voltage
//	} else if (threshold > 255) {
//		threshold = 255;
//	}
	uint32_t threshold = 250;
	if (f_current < 36 * (1ULL << 16)) {
		threshold = 200;
	} else if (f_current < 18 * (1ULL << 16)) {
		threshold = 100;
	} else if (f_current < 12 * (1ULL << 16)) {
		threshold = 30;
	} else if (f_current < 8 * (1ULL << 16)) {
		threshold = 15;
	} else if (f_current < 4 * (1ULL << 16)) {
		threshold = 5;
	}

	/* extract pointer and set new output values */
	uint32_t gpio_reg_write = 0;

	/* set phase U pins */
	uint32_t sign_and_index = phase_accumulator >> 20;
	if((p_current_table[(sign_and_index & 0x7FF)] < threshold) ^ ((sign_and_index >> 11) & 0x1) )
	{
		gpio_reg_write = U_H_Pin;
	}
	else
	{
		gpio_reg_write = U_L_Pin;
	}

	/* set phase V pins */
	sign_and_index = (phase_accumulator+PERIOD_ONE_THIRD) >> 20;

	if((p_current_table[(sign_and_index & 0x7FF)] < threshold) ^ ((sign_and_index >> 11) & 0x1) )
	{
		gpio_reg_write |= V_H_Pin;
	}
	else
	{
		gpio_reg_write |= V_L_Pin;
	}

	/* set phase W pins */
	sign_and_index = (phase_accumulator+PERIOD_TWO_THIRD) >> 20;
	if((p_current_table[(sign_and_index & 0x7FF)] < threshold) ^ ((sign_and_index >> 11) & 0x1) )
	{
		gpio_reg_write |= W_H_Pin;
	}
	else
	{
		gpio_reg_write |= W_L_Pin;
	}

	gpio_reg_write |= ((sign_and_index >> 11) & 1) << 1; // scope trigger
	LL_GPIO_WriteOutputPort(GPIOB, gpio_reg_write);
}


void motor_disconnect(void)
{
	/* connect all phases to GND */
	LL_GPIO_WriteOutputPort(GPIOB, (1 << 8) | (1 << 6) | (1 << 4) );
	while(1);

}
/* USER CODE END 4 */
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


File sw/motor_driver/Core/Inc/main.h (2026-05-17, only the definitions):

#define I_MEAS_Pin LL_GPIO_PIN_1
#define I_MEAS_GPIO_Port GPIOA
#define POT_Pin LL_GPIO_PIN_0
#define POT_GPIO_Port GPIOB
#define TRIG_Pin LL_GPIO_PIN_1
#define TRIG_GPIO_Port GPIOB
#define V_MEAS_Pin LL_GPIO_PIN_2
#define V_MEAS_GPIO_Port GPIOB
#define U_H_Pin LL_GPIO_PIN_3
#define U_H_GPIO_Port GPIOB
#define U_L_Pin LL_GPIO_PIN_4
#define U_L_GPIO_Port GPIOB
#define V_H_Pin LL_GPIO_PIN_5
#define V_H_GPIO_Port GPIOB
#define V_L_Pin LL_GPIO_PIN_6
#define V_L_GPIO_Port GPIOB
#define W_H_Pin LL_GPIO_PIN_7
#define W_H_GPIO_Port GPIOB
#define W_L_Pin LL_GPIO_PIN_8
#define W_L_GPIO_Port GPIOB

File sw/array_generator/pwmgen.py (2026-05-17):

from textwrap import dedent, indent
import numpy as np
import matplotlib.pyplot as plt
import helpers


FILENAME = 'pwm_tab'

PERIOD = 1 << 12
BITS = 8
BASELINE = 0.05
PULSES = (1, 3, 5, 9, 15, 27, 45, 81, 135) # japanese values (135 made up)
PULSES = (1, 3, 5, 9, 15, 25, 41, 67, 109, 177, 299)


def display(pwm):
	pwm1 = helpers.fold4(pwm)
	pwm2 = np.roll(pwm1, pwm1.size // 3)
	t = np.linspace(0, 1, pwm1.size)

	pwm_line = pwm2 - pwm1

	u = helpers.v_avg(pwm_line)

	ax = plt.subplot(311)
	plt.plot(t, pwm1, ds='steps-mid')
	ax = plt.subplot(312, sharex=ax)
	plt.plot(t, pwm2, ds='steps-mid')
	ax = plt.subplot(313, sharex=ax)
	plt.plot(t, pwm_line, t, u, ds='steps-mid')
	plt.tight_layout()
	plt.show()

	a = np.abs(np.fft.rfft(u)) / u.size
	plt.semilogy(a)
	plt.xlim((0, 25))
	plt.ylim((10e-5, 1))
	plt.tight_layout()
	plt.show()


def make_table(period, pulses, bits=8):
	bits1 = (1 << bits) - 1
	tri = helpers.tri_touching(period // 2, 3*pulses)[:period // 4 + 1]
	tri = helpers.tri_normal(period // 2, 3*pulses)[:period // 4 + 1]
	tri2 = helpers.tri_normal(period // 4, 1.5 * pulses)
	tri2 = np.append(tri2, np.sign(tri2[-1]))

	if np.count_nonzero(tri2-tri):
		plt.close()
		plt.plot(tri-tri2)
		plt.show()
		print('AAAAAAAAAAAAAAAA')

	t = np.linspace(0, 0.25, period // 4 + 1, endpoint=True)
	wave = helpers.sin3(t)
	wave = helpers.weird_sin(t)

	lut = np.full_like(t, bits1, dtype=np.int32)
	for a in np.linspace(BASELINE, 1, bits1, endpoint=True):
		lut -= a * wave >= tri


	return lut


def print_c_array(a, name):
	txt = [f'const uint8_t {name}[{a.size}] = {{']

	ln = ['\t']
	for i, val in enumerate(a):
		if not i % 16 and i:
			txt.append(''.join(ln).rstrip())
			ln = ['\t']

		ln.append(f'{val:3d}, ')

	txt.append(''.join(ln).rstrip())
	txt.append('};\n')

	return txt


def main():
	t2 = np.linspace(0, 1, PERIOD, endpoint=False)
	pure = np.sin(2 * np.pi * t2)


	txt = [dedent(f'''\
		#ifndef {FILENAME.upper()}
		#define {FILENAME.upper()}

		#include <inttypes.h>


		#define PERIOD 0x{PERIOD:X}

	''')]


	fig, ax = plt.subplots()
	lines = ax.plot(t2, pure, t2, pure, t2, pure, ds='steps-mid')
	plt.xlim((0, 1))
	plt.pause(0.1)

	for n in PULSES:
		print(f'{n} pulses')

		lut = make_table(PERIOD, n, BITS)

		txt += print_c_array(lut, f'pwm{n}')

		# for i in range(0, 1 << BITS):
		for i in ():
			print(i)
			a = i / ((1 << BITS) - 1) * (1 - BASELINE) + BASELINE
			pwm = i >= lut

			pwm1 = helpers.fold4(pwm)
			pwm2 = np.roll(pwm1, pwm1.size // 3)
			pwm_line = np.roll(pwm2 - pwm1, 7 * pwm1.size // 12)
			u = helpers.v_avg(pwm_line)

			lines[0].set_ydata(a * pure)
			lines[1].set_ydata(u)
			lines[2].set_ydata(10 * (a*pure - u))

			# lines[0].set_ydata(pwm2 - pwm1)
			# lines[1].set_ydata(pwm1 * .5 + .05)
			# lines[2].set_ydata(pwm2 * .5 - .05)

			fig.canvas.draw()
			fig.canvas.flush_events()

			# ---------------------
			# pwm1 = fold2(pwm) # (pwm made from wave2)
			# pwm2 = np.roll(pwm1, pwm1.size // 3)
			# pwm_line = np.roll(pwm2 - pwm1, 7 * pwm1.size // 12)
			# u2 = helpers.v_avg_new(pwm_line)

			# lines[0].set_ydata(10*(a*pure-u2))
			# lines[1].set_ydata(10*(u-u2))

			# fig.canvas.draw()
			# fig.canvas.flush_events()

	plt.close()


	txt.append('#endif\n')
	txt = '\n'.join(txt)

	with open(f'{FILENAME}.c', 'w', encoding='ascii') as f:
		f.write(txt)


if __name__ == '__main__':
	main()

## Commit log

2023-09-24 finished PCB
    [half_bridge.kicad_sch, motor_driver.kicad_pcb, motor_driver.kicad_sch]
2023-10-02 first working version
    [motor_driver.kicad_sch]

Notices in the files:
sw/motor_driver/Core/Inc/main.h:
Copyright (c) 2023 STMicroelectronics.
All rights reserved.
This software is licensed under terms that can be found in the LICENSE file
